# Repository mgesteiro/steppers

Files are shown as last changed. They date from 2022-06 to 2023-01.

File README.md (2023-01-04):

# 28BYJ-48 steppers stuff (WIP)
A recopilation of **28BYJ-48** stepper motor + **ULN2003** driver *experiments*, *checks*, *analysis*, *documentation*, *models* and *data*, mainly for our own knowledge and reference as we use them **a lot** in projects like [**Escornabot Luci**](https://github.com/roboteach-es/escornabot-luci). Feel free to explore the contents of this repository, and if you have any sugestion, please, contact us!

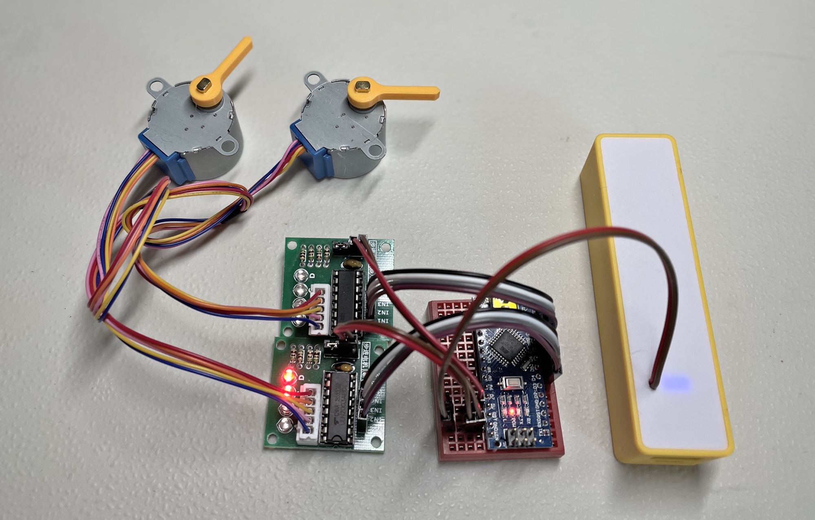
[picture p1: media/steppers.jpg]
steppers


This is the *testing equipment* I've been using: Arduino Nano, 5V Powerbank (modified) and two 28BYJ-48 stepper motor + ULN2003 driver module. [Connection schema](#schemas) available in the `schemas` folder.

## "THE" BIBLE
This is, in my opinion, one of the best explanations about the **28BYJ-48 + ULN2003** stepper motor + driver combo, by [Bret Stateham](https://github.com/BretStateham):

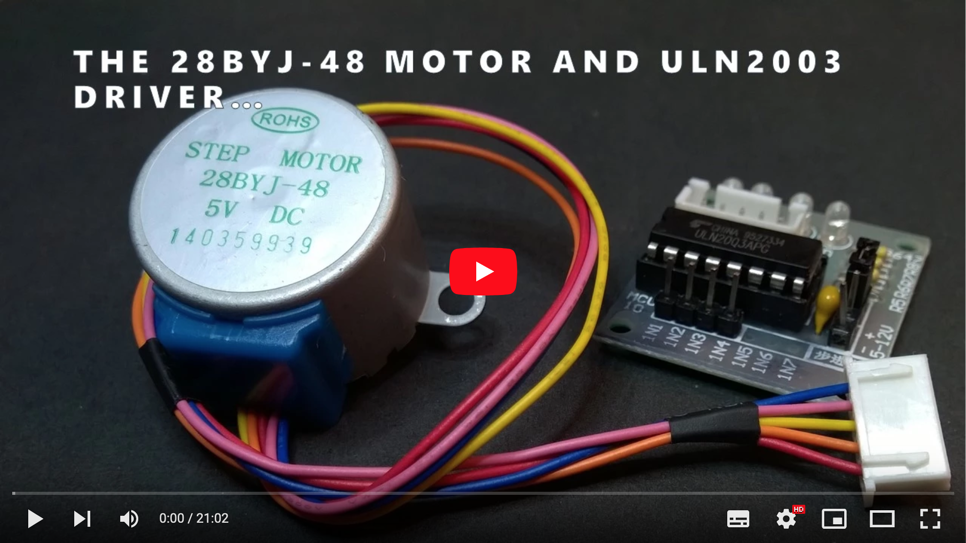
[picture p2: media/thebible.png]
thebible (https://youtu.be/B86nqDRskVU)


There is also a very complete web page with very detailed information and explanations 
about the 28BYJ-48 stepper motor here:
[https://cookierobotics.com/042/](https://cookierobotics.com/042/)

## INFO

28BYJ-48 is an inexpensive unipolar stepper motor with 4 phases and 5 wire connection,
normally driven using a ULN2003 Darlington transistors array IC.

### Gears

The 28BYJ-48 comes with an integrated reduction gear box, available, at least, in two different configurations (ratios): the most common **64:1** and the not so common **16:1**.

(https://cookierobotics.com/042/)

In the most common version, this is how each gear connects with the following (in order):

* Motor shaft: 9 teeth
* 1st gear: 32/11 teeth (32:9 ratio with previous)
* 2nd gear: 22/9 teeth (22:11 ratio with previous)
* 3rd gear: 26/10 teeth (26:9 ratio with previous)
* Output shaft: 31 teeth (31:10 ratio with previous)

	`Final Ratio = 32/9 * 22/11 * 26/9 * 31/10 = ~63,6840  ~64:1`

### Stepping

The motor shaft has attached a cylindrical permanent magnet (8 pairs of north-south
poles). Surrounding it, there are two coils in
[unipolar configuration](https://en.wikipedia.org/wiki/Stepper_motor#Unipolar_motors)
(i.e., with a common middle connection point), which implies 4 different phases.

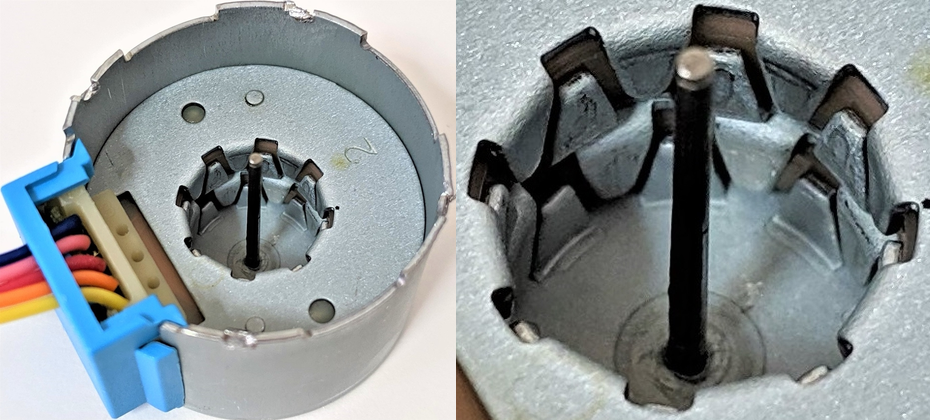
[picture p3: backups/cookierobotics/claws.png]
(https://cookierobotics.com/042/)


The same casing metal is used as the electromagnetic core for the coils:

* 32 small metal tabs (or *claws* or *teeth*)
* spread evenly across 360° (11,25° separate each two tabs)
* intermixed and distributed in two layers (1 per coil): 8x8 - 8x8

**Stepping modes:**
* Wave: one phase each time (4-step sequence)
* Full: two phases each time (4-step sequence)
* Half: alternating one and two phases (8-step sequence)

**Additional stepping info:**
* Internal motor step angle in 4-step sequence: 11.25° (32 steps per revolution)
* Internal motor step angle in 8-step sequence: 5.625° (64 steps per revolution)
* Steps per output shaft revolution in 4-step sequence: 32 * 63,6840 = 2037,8864 (~2038)
* Steps per output shaft revolution in 8-step sequence: 64 * 63,6840 = 4075,7728 (~4076)
* Frequency: 100Hz
* Idle In-traction Frequency: > 600Hz
* Idle Out-traction Frequency: > 1000Hz
* In-traction Torque: > 34.3 mN·m (120Hz) 
* Self-positioning Torque: > 34.3 mN·m
* Friction torque: 600-1200 gf·cm
* Pull in torque: 300 gf·cm

### Electrical characteristics
* Number of phase: 4
* Rated voltage: 5V DC (there are 12V versions too)
* Current consumption (measured at the the ULN2003 driver module entry point): ~165 mA one
  phase powered, ~315 mA two, ~450 mA three, ~570 mA all four
* DC resistance: 50 Ω ± 7% per coil (25°C)
* Insulated resistance: > 10 MΩ (500 V)
* Insulated electricity power: 600 VAC / 1 mA / 1 s
* Insulation grade: A
* Wiring: see the [section bellow](#wiring)

### Other parameters
* Rise in Temperature: < 40 K (120Hz)
* Noise: < 35 dB (120Hz, No load, 10cm)
* Weight: 30g

### Datasheets
Some datasheet documents are available in the `datasheet` folder.

## WIRING
If we *believe* what the \[*only one I could find all over the Internet*\] [28BYJ-48 Datasheet](datasheet/28BYJ-48-5VDC.pdf) says, the wiring should be:

	A (Pink), B (Blue), C (Orange), D (Yellow) and Common/Vcc (Red)

But, in my own experience, the **most common** order is:

	A (Blue), B (Pink), C (Yellow), D (Orange), Common/Vcc (Red)

In the *real world* I've come to find different combinations, where the wiring order comming out of the stepper itself, and the order at the JST connector in the end, may be any of the following:

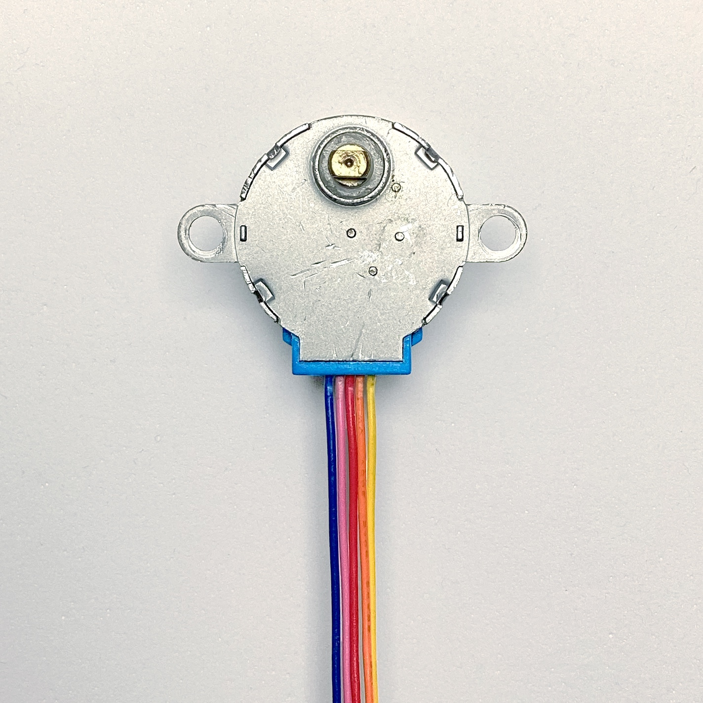
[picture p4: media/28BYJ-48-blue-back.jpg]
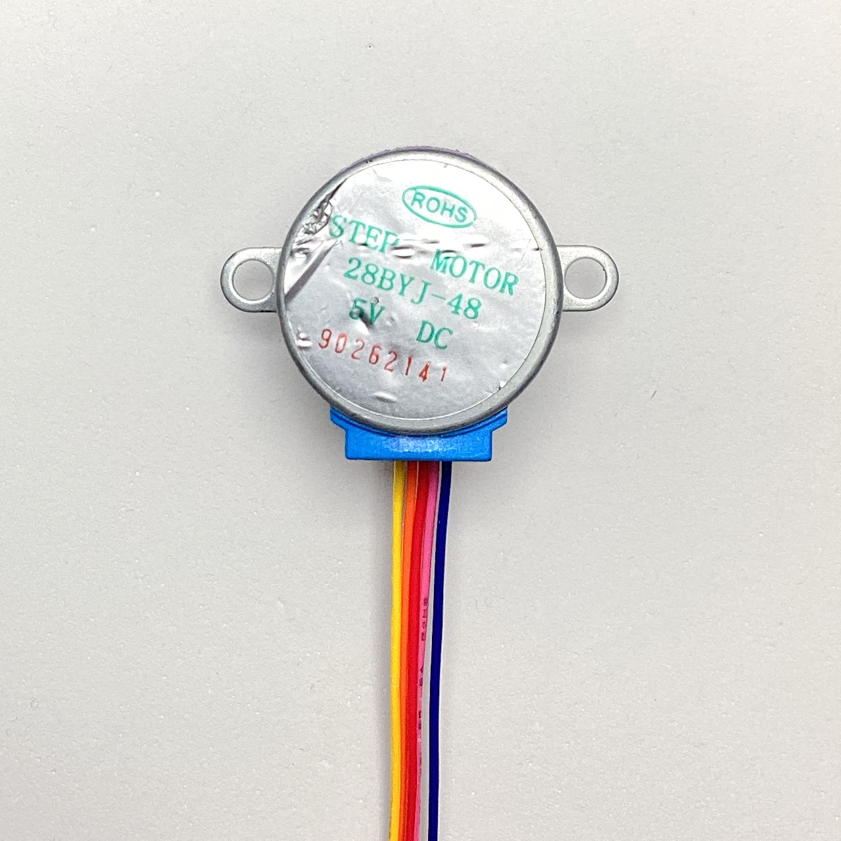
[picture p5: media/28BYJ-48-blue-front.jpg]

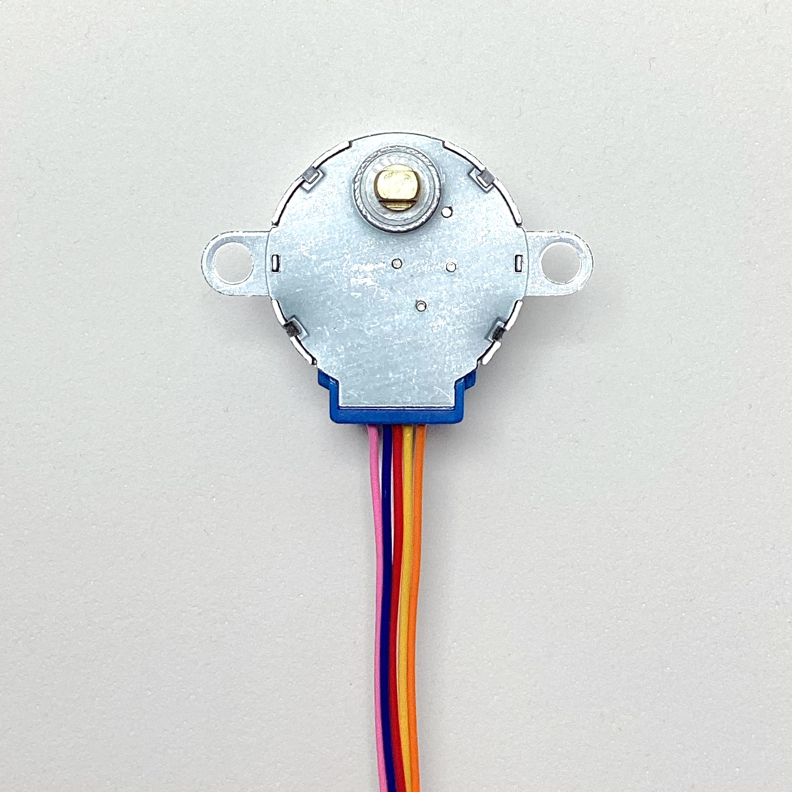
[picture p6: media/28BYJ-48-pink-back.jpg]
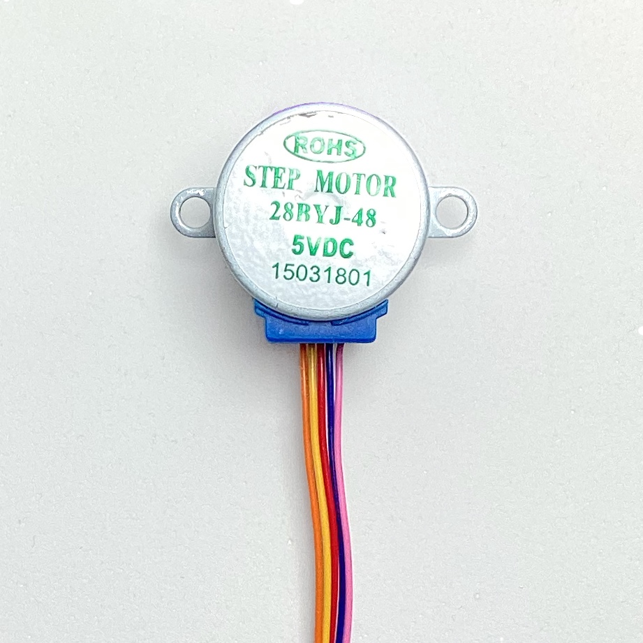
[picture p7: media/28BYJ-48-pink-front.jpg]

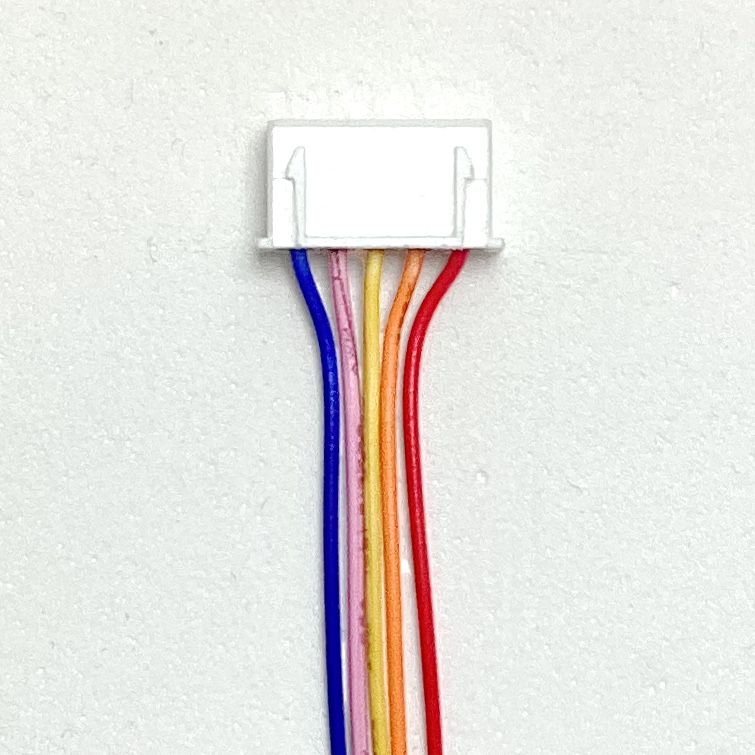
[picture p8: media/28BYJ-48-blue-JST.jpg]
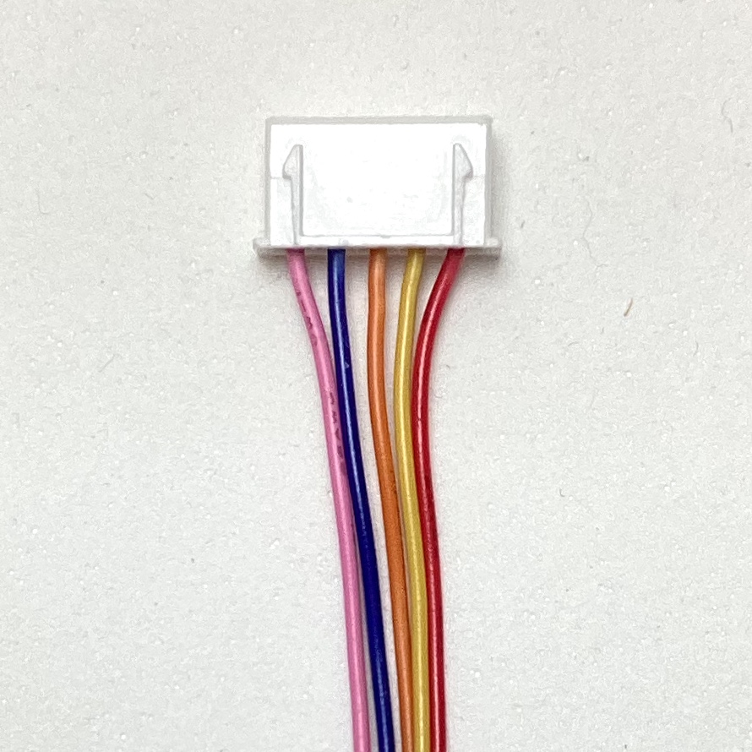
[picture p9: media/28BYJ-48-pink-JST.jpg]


The Red (common/Vcc) wire is always in the same place (middle at the stepper, to the right in the connector), but Blue/Pink and Yellow/Orange may come swapped between them and, depending if they come swapped at both ends or not, you may get different movement (or not).

We've seen really strange/weird *cases*, but usually, in practical terms, the stepper-motors behave in two different ways:

* _**normal**_: i.e., as your code expects (nothing to do)
* _**swapped**_: motors turn inverted (swapp the Blue/Pink and Yellow/Orange coils/pins, in your code or connections, to solve it)

## SCHEMAS

In the `schemas` folder, created with the open-source software [Fritzing](https://fritzing.org):

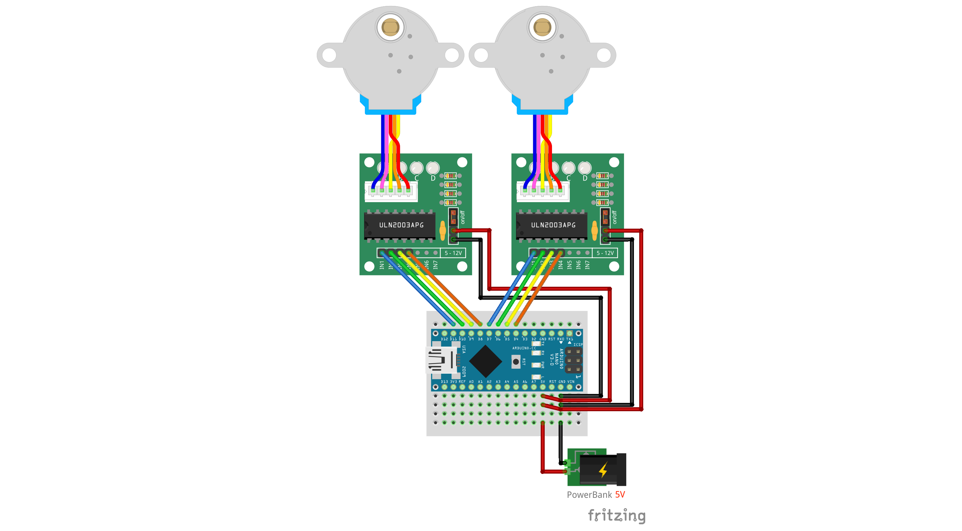
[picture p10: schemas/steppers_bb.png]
schematic


Connection schema of my *testing equipment*.

## CODE

### PORTx vs digitalWrite()

To be able to set the four coils **simultaneously** we can use the [**PORTx registers**](https://docs.arduino.cc/hacking/software/PortManipulation). Also it is a lot faster (2.6x times in my example!) than the [**digitalWrite()**](https://www.arduino.cc/reference/en/language/functions/digital-io/digitalwrite/) counterpart. It's true that the code is more difficult to maintain.

Take a look at the `2X-stepper-portx.ino` and `2X-stepper-digitalwrite.ino` Arduino programs for the comparison:

	Stepper motors (ULN2003 + 28BYJ-48) driving using PORTx registers
	Maximun setCoils() time: 0
	Mode: WAVE  Delay: 2250
	Maximun setCoils() time: 28

	Stepper motors (ULN2003 + 28BYJ-48) driving using digitalWrite()
	Maximun setCoils() time: 0
	Mode: WAVE  Delay: 2250
	Maximun setCoils() time: 72

### WAVE vs FULL vs HALF driving models

There are three ways to drive a **28BYJ-48 stepper motor**. In the `visualize-driving.ino` Arduino program there is a visual demonstration on how the different driving modes operate: steps are executed very slowly so you can see which coils are **on** or **off** every step.

* **WAVE**: 4-step sequence with only one active coil for each step. Good to **save energy**.
* **FULL**: 4-step sequence with two active coils at the same time for every step. Good for the **strongest torque**.
* **HALF**: 8-step sequence with alternating one or two active coils every step. You get the **finest resolution** (2x).

### FULL ROTATION

In **full drive mode**, the theoretical number of steps to perform a full output shaft rotation is **2037,8864** (not even a integer number!), but in the *practical world*, that number is a little higher (**2048**) as you can see in the test code ( `full-rotation.ino`) and the following video:

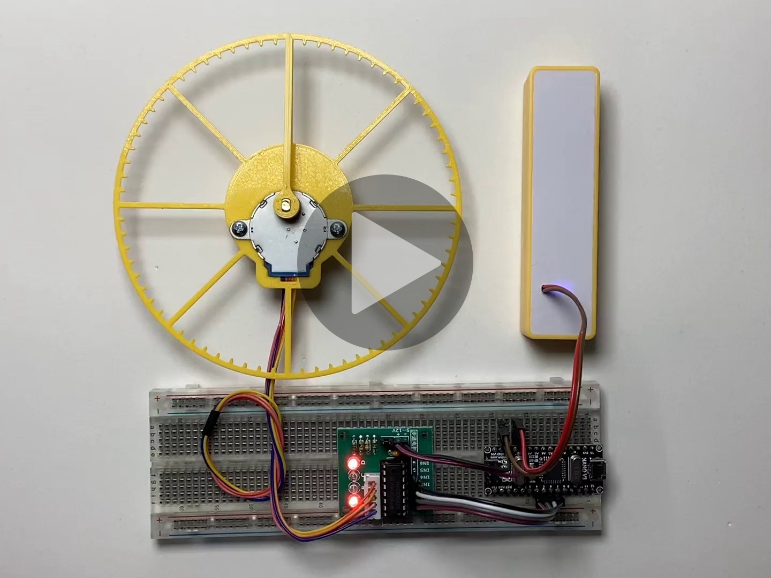
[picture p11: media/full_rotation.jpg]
full rotation video


This difference may be caused by different factors: manufacturing, missed steps, etc. but mostly due to mechanical tolerances. The motor shaft, and the gearbox have some play, as the teeth engagement in every gear with the next isn't perfect, getting up to 4 to 6° of play in the output shaft.

In the [EscornabotEXT](https://gitlab.com/xoan/escornabot-extlib/-/blob/master/src/EscornabotEXT.cpp#L135) and [Mirobot](https://github.com/mirobot/mirobot-arduino/blob/master/src/Mirobot.cpp#L207)'s code, they deal with this issue with _**anti-slack**_ routines.

The code and the 3D printable models for this test are available in their respective folders in case you want to calibrate your own stepper motors.

## 3D models

The **dial** and the **hand** models are available in the [`3D` folder](3D). You can also take a look at my [FreeCAD repository](https://github.com/mgesteiro/FreeCAD-models) for these other models:

28BYJ-48
ULN2003

## Fritzing Parts

Go take a look at my [Fritzing repository](https://github.com/mgesteiro/fritzing-parts) for these parts:

28BYJ-48
ULN2003

## REFERENCES

* Bret Stateham video about the 28BYJ-48 stepper motor + ULN2003 driver module combo: [https://youtu.be/B86nqDRskVU](https://youtu.be/B86nqDRskVU)
* Bret Stateham github: [https://github.com/BretStateham](https://github.com/BretStateham)
* CookieRobotics info about the 28BYJ-48 stepper motor: [https://cookierobotics.com/042/](https://cookierobotics.com/042/)
* Unipolar configuration for stepper motors: [https://en.wikipedia.org/wiki/Stepper_motor#Unipolar_motors](https://en.wikipedia.org/wiki/Stepper_motor#Unipolar_motors)
* **PORTx registers** (a.k.a. PORT manipulation) in Arduino: [https://docs.arduino.cc/hacking/software/PortManipulation](https://docs.arduino.cc/hacking/software/PortManipulation)
* **digitalWrite()** in Arduino: [https://www.arduino.cc/reference/en/language/functions/digital-io/digitalwrite/](https://www.arduino.cc/reference/en/language/functions/digital-io/digitalwrite/)
* BitMath Arduino tutorial: [https://playground.arduino.cc/Code/BitMath/](https://playground.arduino.cc/Code/BitMath/)
* My FreeCAD 3D models repository: [https://github.com/mgesteiro/FreeCAD-models](https://github.com/mgesteiro/FreeCAD-models)
* My Fritzing parts repository: [https://github.com/mgesteiro/fritzing-parts](https://github.com/mgesteiro/fritzing-parts)
* **FreeCAD** 3D CAD modelling software: [https://www.freecad.org](https://www.freecad.org)
* **Fritzing** schematics and PCB modelling software: [https://fritzing.org](https://fritzing.org)

## LICENSE

This work is licensed under the [GNU General Public License v3.0](LICENSE-GPLV30). All media and data files that are not source code are licensed under the [Creative Commons Attribution 4.0 BY-SA license](LICENSE-CCBYSA40).

More information about licenses in [Opensource licenses](https://opensource.org/licenses/) and [Creative Commons licenses](https://creativecommons.org/licenses/).

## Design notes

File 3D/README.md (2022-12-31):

# 28BYJ-48 steppers stuff - 3D models

There are a couple of 3D models here, created with the ope-source software [FreeCAD](https://freecad.org):

* An indexed dial divided in 5 degrees steps:

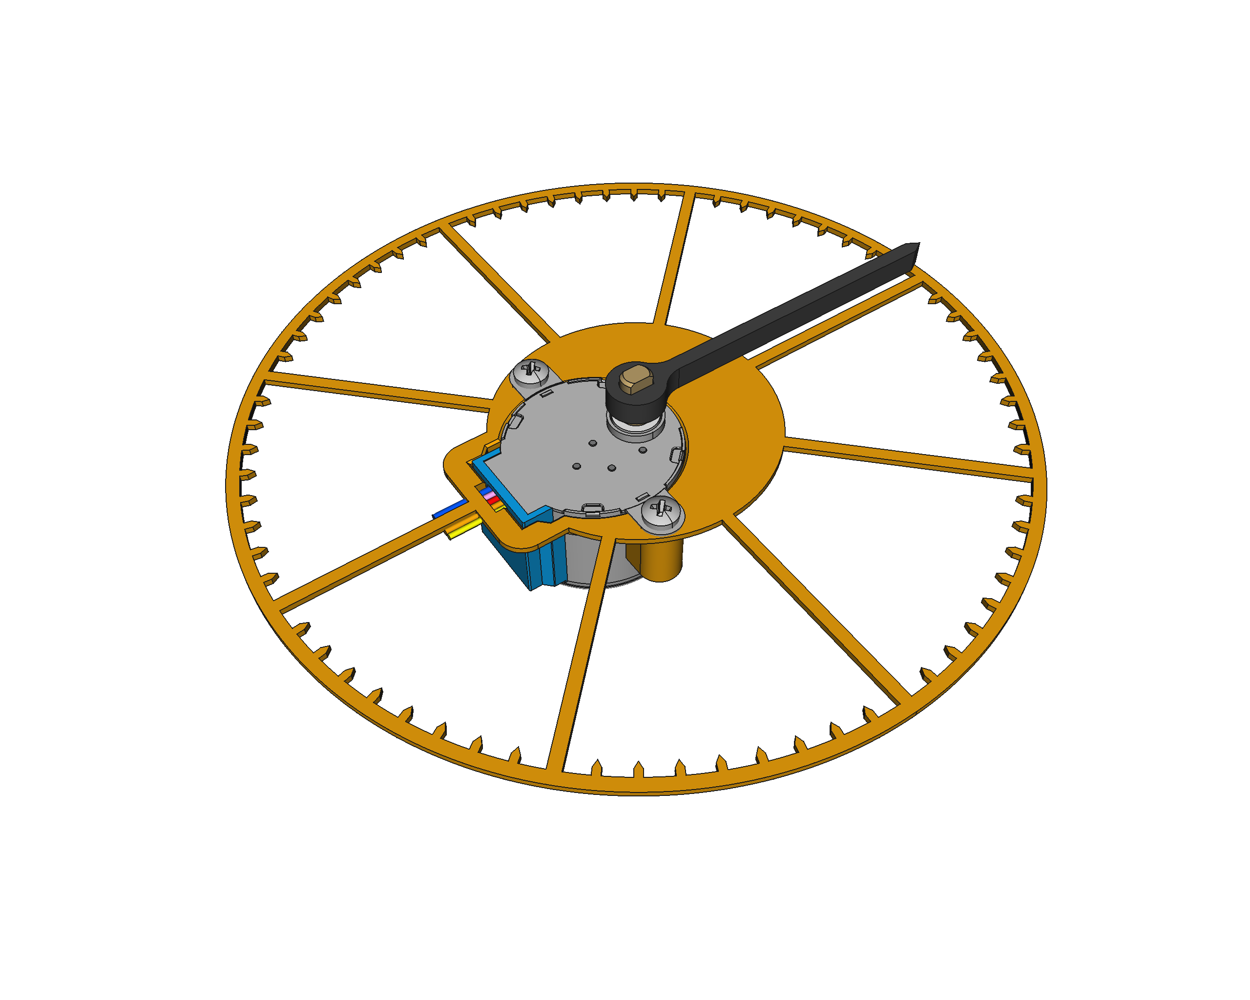
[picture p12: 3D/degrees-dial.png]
Degrees Dial


* The stepper hand in short and long format:

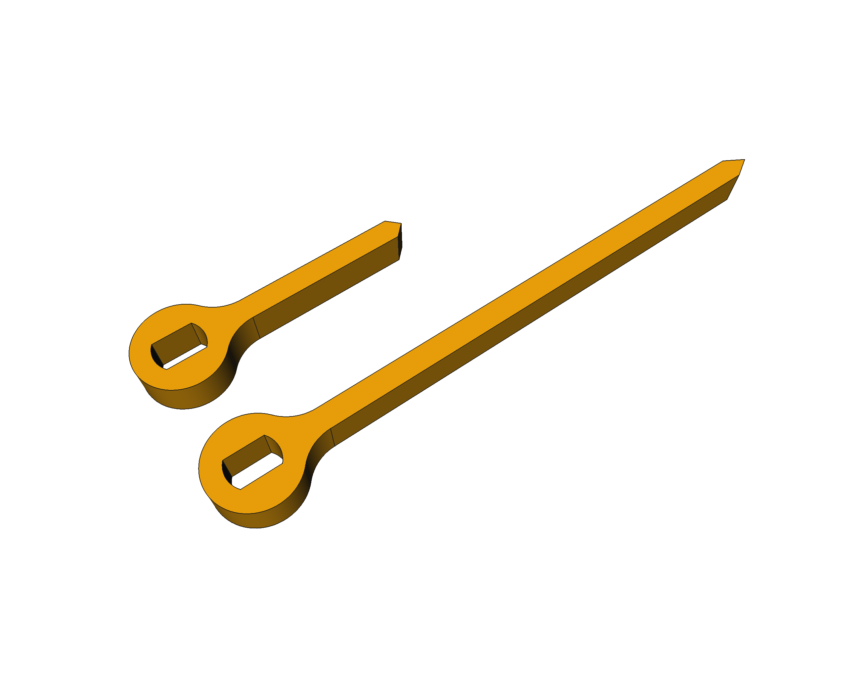
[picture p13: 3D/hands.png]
Hands


All already available in **STL** format, ready to be 3D printed.

## LICENSE

This work is licensed under the [GNU General Public License v3.0](LICENSE-GPLV30). All media and data files that are not source code are licensed under the [Creative Commons Attribution 4.0 BY-SA license](LICENSE-CCBYSA40).

More information about licenses in [Opensource licenses](https://opensource.org/licenses/) and [Creative Commons licenses](https://creativecommons.org/licenses/).

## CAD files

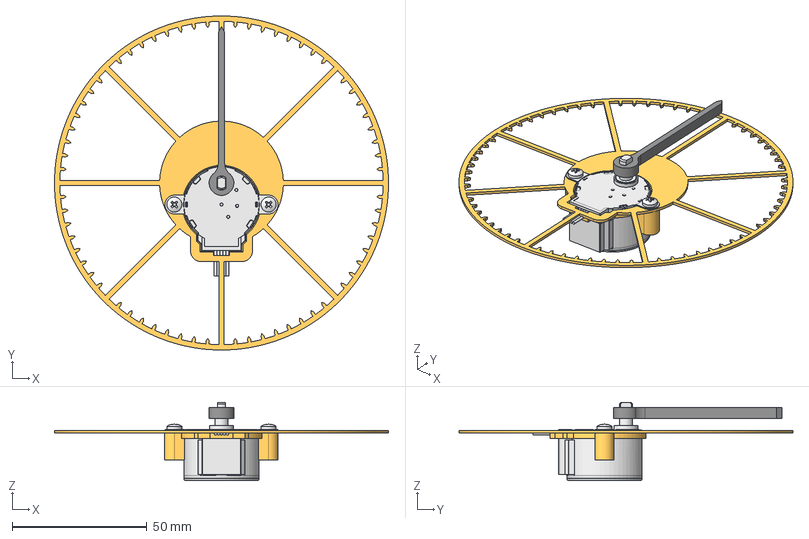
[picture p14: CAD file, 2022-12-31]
3D/degrees-dial.FCStd
124.0 x 124.0 x 29.0 mm
Body-degrees-dial
28BYJ-48-L
hand
M3x10-Screw001
M3x10-Screw

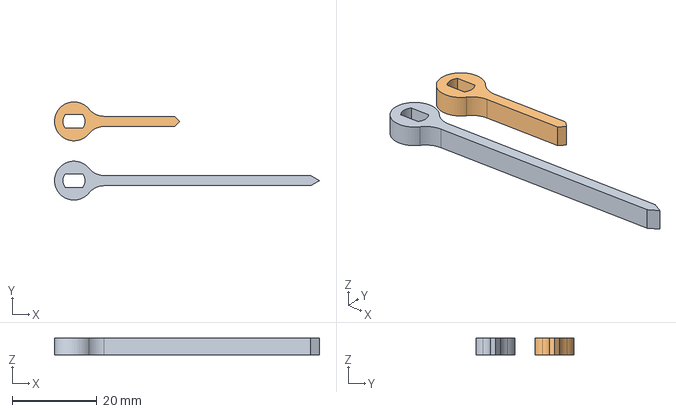
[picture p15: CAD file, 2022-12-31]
3D/hands.FCStd
62.6 x 23.2 x 4.00 mm
Body-long
Body-short

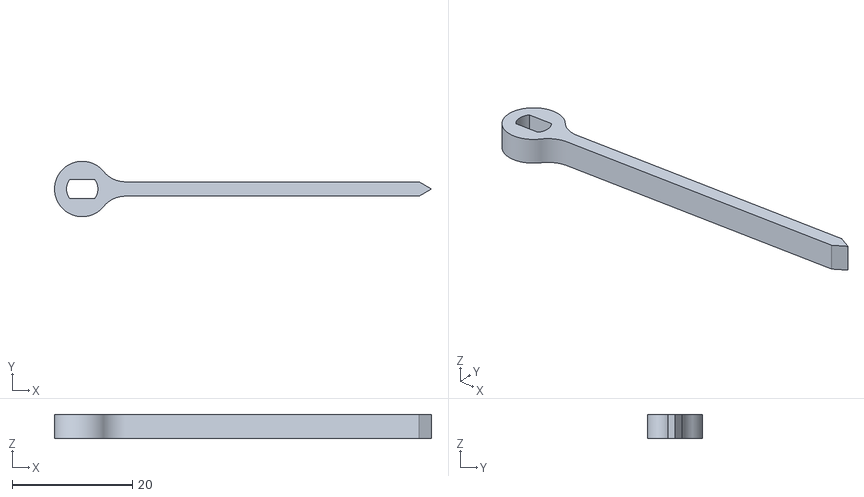
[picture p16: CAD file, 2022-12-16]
3D/hand-long.stl
62.6 x 9.20 x 4.00

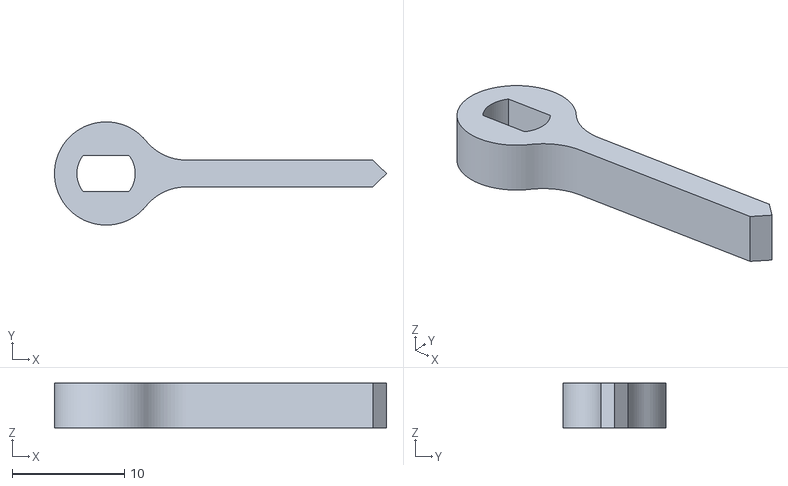
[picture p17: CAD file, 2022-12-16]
3D/hand-short.stl
29.6 x 9.20 x 4.00

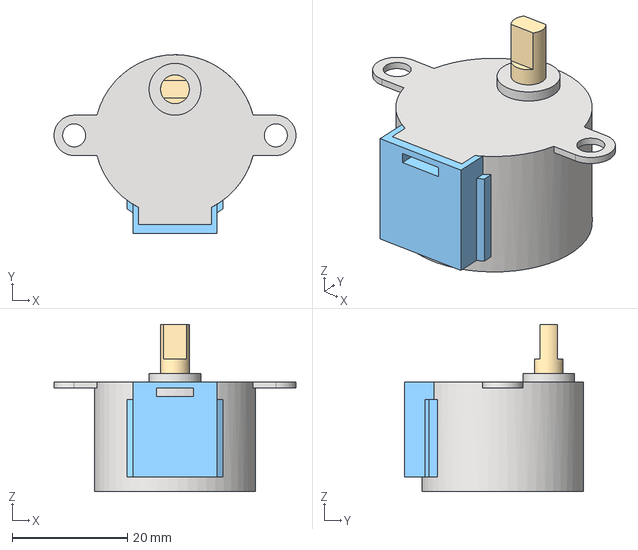
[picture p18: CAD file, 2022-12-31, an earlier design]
backups/cookierobotics/28BYJ-48.step
42.0 x 31.0 x 29.0 mm

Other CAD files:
3D/degrees-dial.stl

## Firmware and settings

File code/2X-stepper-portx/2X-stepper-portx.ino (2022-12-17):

/*
 * Test 2X stepper motors using direct access via DDRx,PORTx and PINx registers
 *
 * https://docs.arduino.cc/hacking/software/PortManipulation
 * https://idyl.io/arduino/how-to/manipulate-arduino-ports/  <-- INPUT_PULLUP using DDRx
 * https://playground.arduino.cc/Code/BitMath/
 * http://graphics.stanford.edu/~seander/bithacks.html
 *
 */

const static uint8_t states_sequences[][8] = {
	{ B0001, B0010, B0100, B1000, B0001, B0010, B0100, B1000 }, // wave drive - repeated 2x
	{ B0011, B0110, B1100, B1001, B0011, B0110, B1100, B1001 }, // full drive - repeated 2x
	{ B0001, B0011, B0010, B0110, B0100, B1100, B1000, B1001 }  // half drive
};
const static char states_sequences_names[][5] = { 
	"WAVE\0", 
	"FULL\0", 
	"HALF\0"
};

const static unsigned int delays[] = { 
	2250, // wave 
	2100, // full
	1050  // half
}; 

// step tracking
int targetSteps = 2048;
int currentStep = targetSteps; // to start-over and get status display

// driving mode
int currentMode = 2; // to start-over and get status display
unsigned int stepDelay = delays[currentMode];

// timing
unsigned long timen=0, timef = 0;


/*
 *   S U P P O R T   F U N C T I O N S
 */

void initCoilsPins()
{
	// PORTB maps to Arduino digital pins 8 to 13. The two high bits (6 & 7) map to the crystal pins and are not usable.
	DDRB = DDRB | B00001111;  // pins x,x,x,x,11,10,9,8 as OUTPUT - Right motor
	// PORTD maps to Arduino digital pins 0 to 7. Pins 0 and 1 are TX and RX, manipulate with care.
	DDRD = DDRD | B11110000;  // pins 7,6,5,4,x,x,x,x as OUTPUT - Left motor

}

void setCoils(uint8_t stateR, uint8_t stateL)
{
	// PORTB maps to Arduino digital pins 8 to 13 The two high bits (6 & 7) map to the crystal pins and are not usable
	// RightMotor - pins 11,10,9,8 -> PORTB bits[3-0] = stateR bits[3-0]
	// (a & ~mask) | (b & mask)
	// a -> PINB  b->stateR  mask->B00001111
	PORTB = (PORTB & B11110000) | (stateR & B00001111);

	// PORTD maps to Arduino digital pins 0 to 7
	// LeftMotor - pins 7,6,5,4 -> PORTD bits[7-4] = stateL bits[3-0]
	// (a & ~mask) | (b & mask)
	// a -> PIND  b->(stateL << 4)  mask->B11110000
	PORTD = (PORTD & B00001111) | (stateL << 4); // implicit mask in second part
}


/*
 *   S E T U P   &   L O O P
 */

void setup() {
	Serial.begin(115200);
	Serial.println("Stepper motors (ULN2003 + 28BYJ-48) driving using PORTx registers");
	initCoilsPins(); 
	setCoils(0, 0);  // disable coils
}

void loop() {
	// tracking the current step we are on
	currentStep++;
	if(currentStep >= targetSteps) {
		setCoils(0, 0);  // disable coils
		currentStep = 0;
		++currentMode %= 3; // change mode
		stepDelay = delays[currentMode];
		// status display
		Serial.print("Maximun setCoils() time: ");
		Serial.println(timef);
		Serial.print("Mode: ");
		Serial.print(states_sequences_names[currentMode]);
		Serial.print("  Delay: ");
		Serial.println(stepDelay);
		delay(1000);
	}
	// action
	timen=micros();
	setCoils(
		states_sequences[currentMode][currentStep % 8],
		states_sequences[currentMode][currentStep % 8]
	);
	timen = micros() - timen;   
	if (timen>timef) timef=timen;
	delayMicroseconds(stepDelay);
}

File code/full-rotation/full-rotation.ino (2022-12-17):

/*
 * Experiment with number of steps for a full rotation of a
 * 28BYJ-48 stepper motor + ULN2003 driver board
 *
 */

const uint8_t STATE_SEQUENCE[] = {B0011, B0110, B1100, B1001}; // full drive
const uint8_t MAX_STATE_SEQUENCE = sizeof(STATE_SEQUENCE) - 1;

void initCoilsPins()
{
	// PORTD maps to Arduino digital pins 0 to 7. Pins 0 and 1 are TX and RX, manipulate with care.
	DDRD = DDRD | B11110000;  // pins 7,6,5,4 as OUTPUT - Left motor
}

void setCoils(uint8_t state)
{
	// PORTD maps to Arduino digital pins 0 to 7
	// Motor - pins 4,5,6,7   -> PORTD bits[7-4] = state bits[3-0]
	// (a & ~mask) | (b & mask)
	// a -> PIND  b->(state << 4)  mask->B11110000
	PORTD = (PORTD & B00001111) | (state << 4); // implicit mask in the second part
}

void doSteps(int16_t howmany)
{
	uint8_t seq_index = 0;
	for (int i=0; i<howmany; i++)
	{
		setCoils(STATE_SEQUENCE[seq_index]);
		seq_index ++;
		if (seq_index > MAX_STATE_SEQUENCE) seq_index = 0;
		delayMicroseconds(2000);
	}
}

void setup() {
	initCoilsPins();
	delay(1000);
}

void loop() {
	// Theoretical value: 32 * 63,6840 = 2037,8864
	// Practical value: 2048 (slips, gear teeth engagement, etc.)
	doSteps(2048*4); // various rotations to appreciate the drift
	delay(2000);
}

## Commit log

2022-06-20 First files and code
    [indicator.FCStd, indicator.stl, stepper.fzz]
2022-06-23 Added new visualizing code and images
    [indicator.FCStd, indicator.stl, stepper.fzz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]
2022-12-16 New 3D model and updted url
    [degrees-sphere.FCStd, degrees-sphere.stl, indicator-long.stl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]
2022-12-17 PORTx manipulation error fixed
    [2X-stepper-portx.ino, full-rotation.ino]
2022-12-31 updated info and some backups
    [28BYJ-48.step, degrees-dial.FCStd, degrees-dial.stl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]
